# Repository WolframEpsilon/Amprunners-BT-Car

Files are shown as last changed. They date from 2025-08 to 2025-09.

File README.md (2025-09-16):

# ⚡ The Amprunners BT Car Project  
## Table of Contents
1. [Project Overview](#project-overview)  
2. [Components Used](#components-used)  
3. [Circuit Design](#circuit-design)  
4. [Code Implementation](#code-implementation)  
5. [Chassis & Assembly](#chassis--assembly)  
6. [Testing & Challenges](#testing--challenges)  
7. [Future Improvements](#future-improvements)  
8. [Credits](#credits)  

---

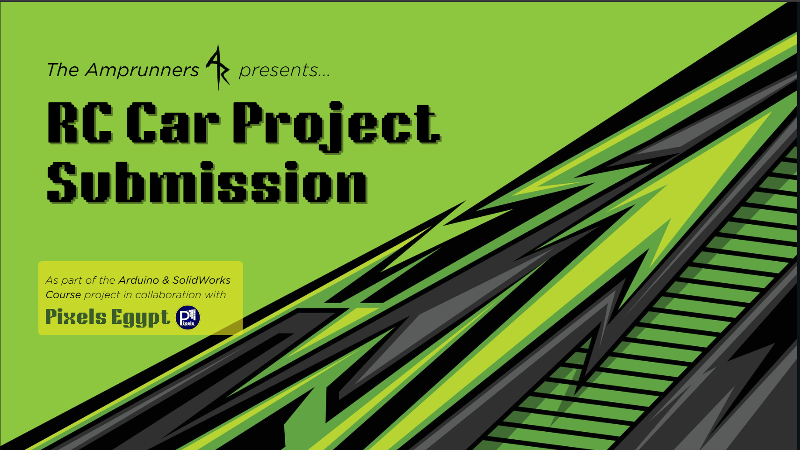
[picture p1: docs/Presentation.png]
Canva Design (https://www.canva.com/design/DAGyNDEWMuc/WyMPQTmzuohv-2UcNLUx6A/view?utlId=hdddcee9b77#1)


> A course project built to demonstrate skills in electronics, microcontroller programming, and system integration.  

---

## Project Overview
This project was developed as part of a Pixel's Embedded Arduino and SolidWorks course to design and build a working toy car.

The goal was to build two cars from scratch, control them wirelessly using:
* Bluetooth module (as used in model APEX)  
* Mobile BT App (seen in model NOVA)
  
### [📱 Amprunners Controller App (Android)](Amprunners_controller.apk)
### [🎥 Watch Demo Video (MP4)](docs/Demo.mp4)
---

## Components Used 
**3D model, wheels, chassis and assembly have their own section below*
- **Microcontroller:** Arduino Uno R3 (Car control)
- **Motor Driver:** L293D H-Bridge  
- **Motors:** 2x DC hobby motors (for RWD)
- **Steering:** SG90 micro servo motor
- **Sensors:** HC-SR04 ultrasonic (for obstacle detection)  
- **Communication:** HC-05 Bluetooth module 
- **Power:** 3.7V Li-ion battery x 3  
- **Sound:** TMB12A05 Active buzzer, KSP2222A Transistor
- **LEDs:** 3 pairs (red, white, and 3rd's your colour of choice) 
## Extra components for model APEX:
- **Control:** KY-023 PS2 joystick module
- **Microcontroller:** A second Arduino Uno R3 (Remote control) 
- **Communication:** HC-05 Bluetooth module 

---

## Circuit & System Design
#### Wiring Diagram 
- Wiring on [TinkerCAD](), or view the circuit as a [.brd file](hardware/circuit.brd)
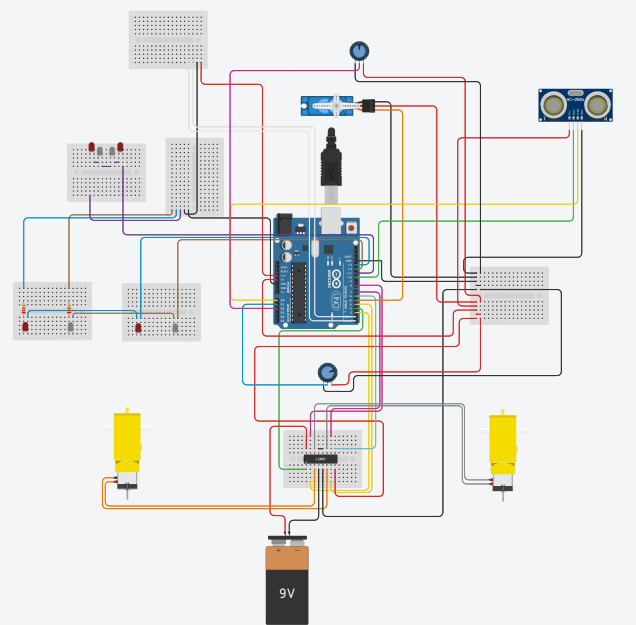
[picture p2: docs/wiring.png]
Wiring Diagram
-

#### Power distribution: 
*connecting the 3 batteries in series using a pack*

    Battery pack --> Kill switch --> H-Bridge +12V pin
    H-Bridge 5V pin --> 5V power rail --> Arduino's 5V power pin 
  <small>(more on this later)</small>  

### Pin Connections: 

##### Motors
| Component | Pin / Connection |
|---|---|
| Motor A IN1 | D3 |
| Servo Control | D4 |
| Motor A IN2 | D5 |
| Motor B IN1 | D6 |
| Motor B IN2 | D9 |

##### Comms.
| Component | Pin / Connection |
|---|---|
| BT Module Tx | D0 (MCU Rx) |
| BT Module Rx | D1 (MCU Tx) |
| Ultrasonic Trig | D8 |
| Ultrasonic Echo | A0 |

##### Others
| Component | Pin / Connection |
|---|---|
| Transistor (buzzer) | D2 |
| HeadLights | D11 |
| Reverse Lights | D12 |
| Taillights | D13 |

---

## Code
Main features of the code:
- Reads instructions from BT module/App.  
- Controls motors' speed (3 in each direction) via H-Bridge.
- Control steering via servo motor (front wheels) + one hobby motor (rear wheel)   
- Stops when obstacles are detected by ultrasonic, then starts beeping.
- Beeps periodically when backing up (like big trucks)
- Toggling on/off headlights and buzzer (horn)
- Reverse and Tail lights light up automatically according to movement 

#### *Code Snippet* 
##### [Full NOVA code available here](/src)
```cpp

switch (read){
  case 'F':  
    if(!stopFlag){
      forward(); digitalWrite(backled,LOW); digitalWrite(buzz,LOW);}
    else{
      stop(); digitalWrite(backled,HIGH); buzzAlert();}
      break;

  case 'B': 
    digitalWrite(backled,LOW); backward(); buzzRev(); ledRev(); 
    break;  
``` 
<sub>IDE: Arduino IDE 
Libraries: Servo.h   
Board: Arduino Uno R3   
Baud rate: 9600 baud   
</sub>   

---

## Chassis & Assembly 
Our team agreed on making the car RWD, rather than AWD; simply because it was more economical

> Using [this model](https://www.thingiverse.com/thing:4772279) made by Pammeg80 on Thingiverse.com as our inspiration , with some slight adjustments

#### Alterations to base model:
1. Made a small hole using SolidWorks to fit the pins for the ultrasonic sensor
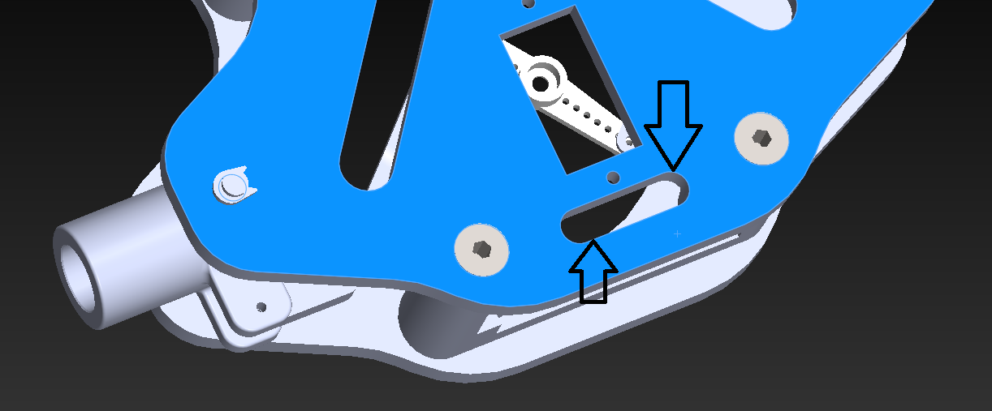
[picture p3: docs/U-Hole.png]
Ultrasonic Hole adjustment
-

2. Removed the 9V power at the back, while mounting the 12V pack (mentioned here) under the model 
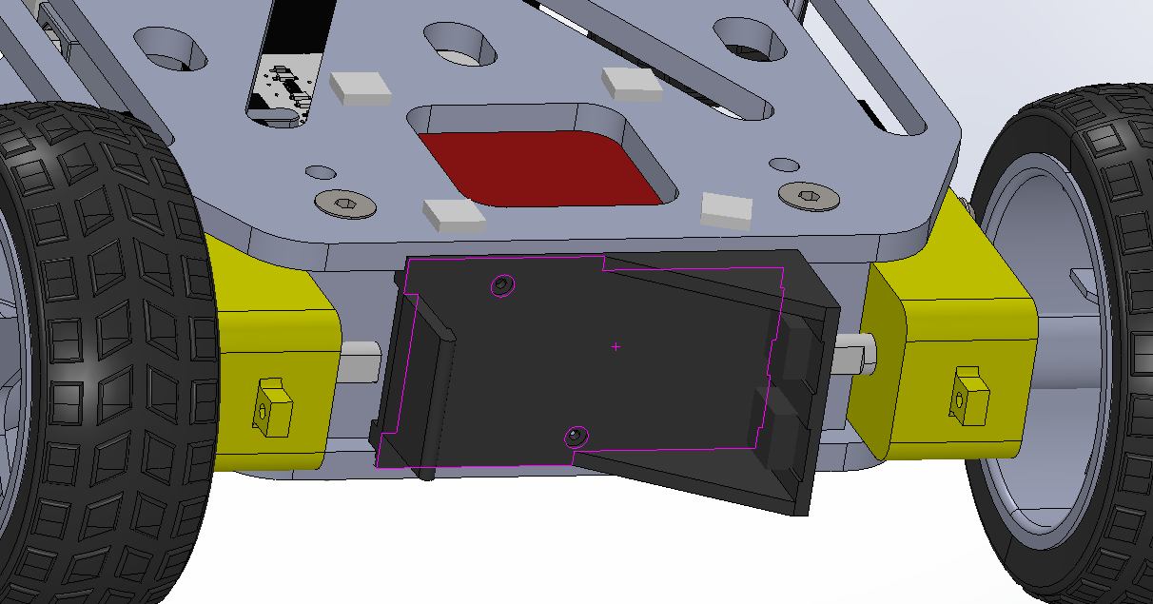
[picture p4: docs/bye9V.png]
9V removal
-

3.  Adding a nameplate for visuals with a "THOMAS" text ingravement + LED Holes 
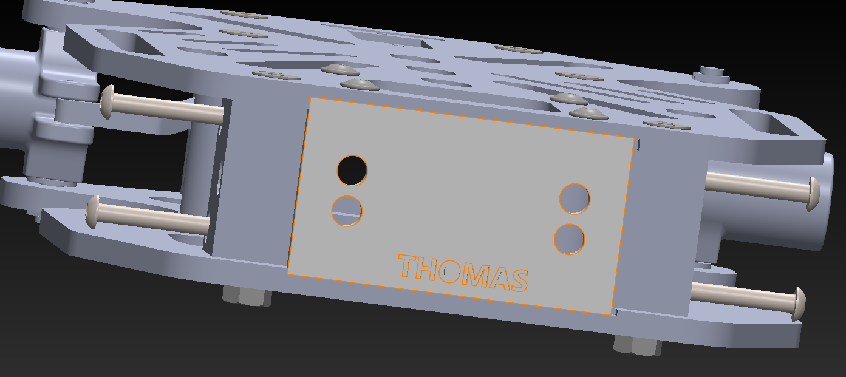
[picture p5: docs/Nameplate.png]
Thomas Nameplate
-

4. Small pillars to hold headlight's LEDs (Not saved unfortunately)  

---

## Testing
### Phase 1: Wiring test
This was done by adding a Keyboard (of varing resistance) to one analogue pin, and manually taking resistance reading to form a resistance-to-key map.
The following map was created:

```cpp
//Keypad Resistance Map//
#define ast_KEY 47
#define zero_KEY 51
#define hash_KEY 57
#define seven_KEY 60
#define D_KEY 64
#define eight_KEY 68
#define nine_KEY 79
#define four_KEY 85
#define C_KEY 93
#define five_KEY 102
#define six_KEY 128
#define one_KEY 146
#define B_KEY 171
#define two_KEY 205
#define three_KEY 341
#define A_KEY 1023

#define keyPin A1 //where i received the key strokes
```

Analogue pins are know to give a range of values due to external factors, like temperature changes messing with the resistance reading
So a tolerance range was added to compensate for this error as shown in this function:

```cpp
//funcion for reading the keypad-resistance configuration//
char KeypadReading() {
  int val = analogRead(keyPin);

  // sorted in ascending order with tolerances of 2~4//
  if (val < 44) return 0;  //null if not in range//  
  else if (val < 49) return '*';
  else if (val < 53) return '0';
  else if (val < 59) return '#';
  else if (val < 62) return '7';
  else if (val < 66) return 'D';
  else if (val < 70) return '8';
  else if (val < 82) return '9';
  else if (val < 88) return '4';
  else if (val < 96) return 'C';
  else if (val < 105) return '5';
  else if (val < 132) return '6';
  else if (val < 150) return '1';
  else if (val < 175) return 'B';
  else if (val < 210) return '2';
  else if (val < 345) return '3';   
  else if (val > 1000 && val <= 1023) return 'A';

  return 0; //again, null if not in range//
}
``` 

### Phase 2: Joystick Implementation
Using a potentiometer (10K Ohm) for steering control, and another (10K Ohm) for motor speed we constructed the following circuit:
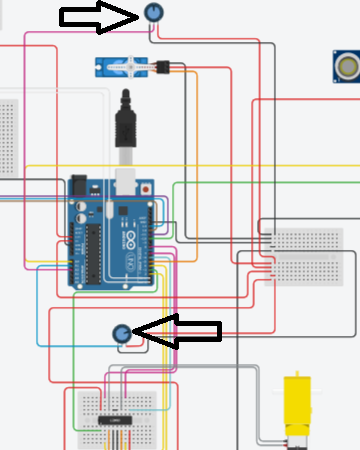
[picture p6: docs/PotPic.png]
Potentiometer circuit
-   

and controlled their movement using the code below: 
```cpp
  int steer = map(analogRead(steerPot),0,1023,0,180); //joystick reading for servo
  int drive = map(analogRead(hobbyPot),0,1023,0,255); //joystick reading for motor
  
  Serial.print("steer= ");
  Serial.print(steer);
  Serial.print("||drive= ");
  Serial.println(drive);
  
  //-----front and back in 3 levels each-----//
  if(drive == 128) {  // ~centered
    digitalWrite(backLED,HIGH);  //not moving
    digitalWrite(reverseLED,LOW); //reverse-light off
  }
  else if(drive > 128){ //going forwards
    forwards(drive); 
    digitalWrite(backLED,LOW); //break-light off
    digitalWrite(reverseLED,LOW); //reverse-light off
  }
  else if(drive < 128){ //going backwards
    backwards(drive); 
    digitalWrite(backLED,LOW); //break-light off
    digitalWrite(reverseLED,HIGH); //reverse-light on
  }

  //-----right and left-----//
  steerMotor.write(steer);
```

---

## Challenges (and how we overcame them)

## 1. 12V power to 5V Arduino:
#### Issue:
>* Feeding 12V into the arduino power plug would instantly fry the circuit
>* using multiple power sources would be inefficient and require extra wiring complexity
>* Linear voltage regulator need comprehensive understanding (in a small time period)
### Solution: H-bridge power supply
Surprisingly, the **L293D H-Bridge** model has a neat feature activated by adding a jumper cap to a built-in voltage regulator; allowing +12V power to motors and feeding just 5V from it's power slot (normally used to power the module itself)

## 2. H-bridge driving wheels incorrectly
This manifested as both RWD motors being able to move backwards, but motor A (left) failing to drive forwards
#### Cause: 
>Instability from mechanical vibration of motors; resulting in lose conections
#### Solution: Physically fixing connections and insulation
using a hot soldering iron and lead, we were able to Solder connections well, and prevent shorts using Heat shrink tubing at exposed locations

## 3. Car wheels not fitting into chasis
#### Cause:
>no tolerances added during modelling; which lead to an impossible interference fit
#### Solution: Tolerance adjustment 
fortunately, we had a drill bit that was exactly the same size as the wheel, so we manually drilled through 

## 4. Irresponsive Bluetooth Pair (with remote control)
#### Cause:
>modules aren't always recognised by smart devices at specific ports, and won't go into pair or AT mode when enabled by pin
#### Solution: Changing baud rate 
It's more of a compatability problem across devices where serial communication is set out of sync, eg. 9600 baud Uno with 11600 BT module

## Other challenges
- Servo motor torque limitations occasionally caused unintended steering drift (sometimes leading to unplanned donuts 😅)
  -Thomas going wild

- Connecting pins and general wiring in the chassis; which is an extremely small area, sometimes inaccessible without t6aking the whole thing apart again

- Weak arduino pin connection, affected by the motors' vibration 

- Exposed wiring <small> (in future improvements) </small>
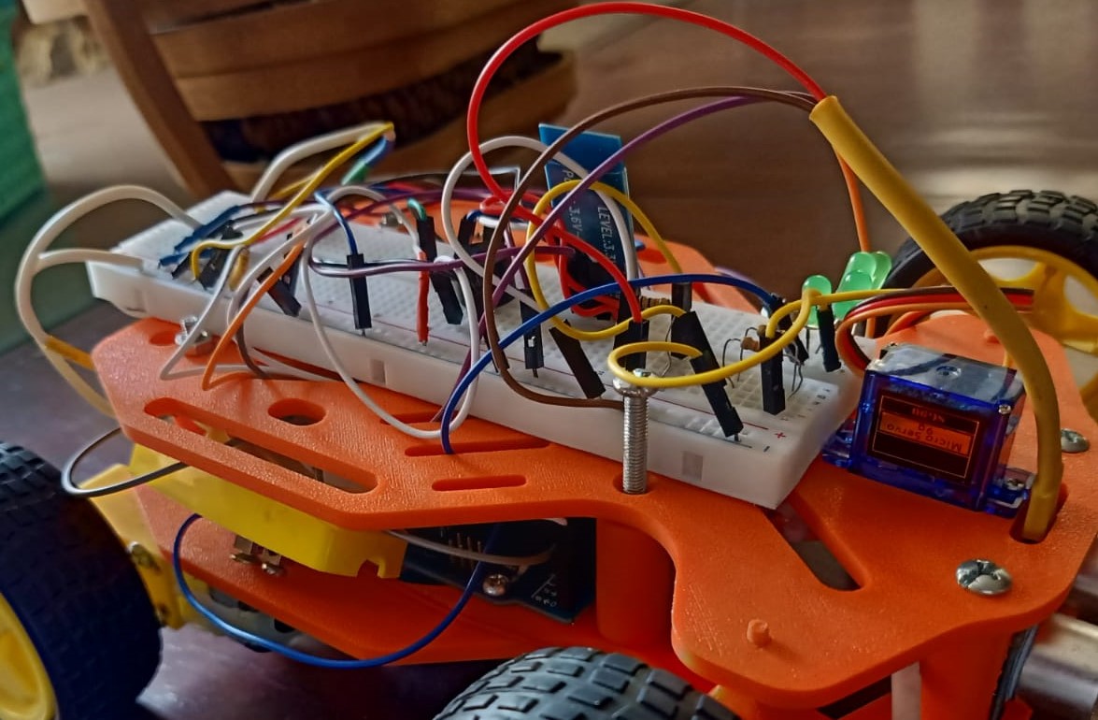
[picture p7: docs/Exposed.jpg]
Exposed
  -
---

## Future Improvements
### 1. Using an ESP32 MCU
- Built-in BT and WiFi
- More pins and faster clock speed
- Smaller footprint in an already crammed area
### 2. 3D Printing the car's original body
We didn't have the time to assemble this part withing the deadline, but we do have the model (pulled from Rocket League by [Paul Ashley on GrabCAD](https://grabcad.com/library/all-rocket-league-car-object-files-a-few-bonus-s-1)):
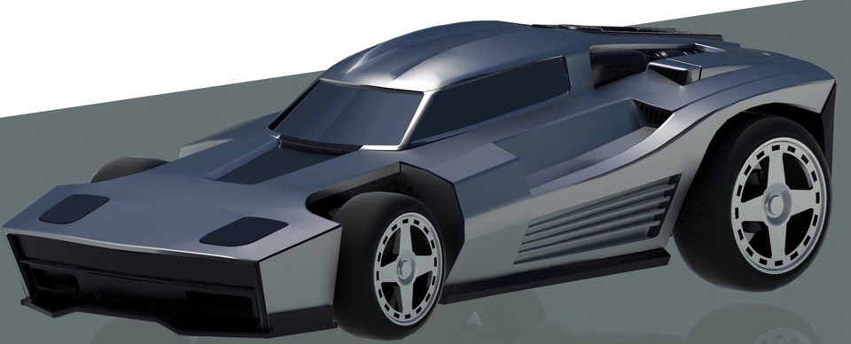
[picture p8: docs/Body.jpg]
Body
  -
### 3. Backwards Obstacle Detection
reducing impact possibility, thus improving lifespan 
### 4. Surface-mounted robotic arm  
for object transportation, perhaps in warehouses
### 5. Infrared light sensor
for line follower feature
### 6. Camera Module
for object distinction or QR code scanning

---

## Credits
#### [Omar M. Gobara](www.linkedin.com/in/omargobara/)
* Full Simulation (TinkerCAD)
* Final Assembly & Code Polishing
* Documentation (this one) 
* Body prototype

#### [Ahmed I. Madkour](https://www.linkedin.com/in/ahmedimadkour/)
* 3D modelling (SolidWorks) & Printing
* initial Assembly & Code integration
* Project management & Team coordination
* Cosmetics Design (Presentation, Logos, IDs, etc.)

#### [Kerollos Mekhail](https://www.linkedin.com/in/kerollos-mekhail-gad/) 
* Lead Custom application developer (MIT App Inventor)
* Car BT Communication Subsystem
* Car Speed Subsystem

* intermediate Code developer

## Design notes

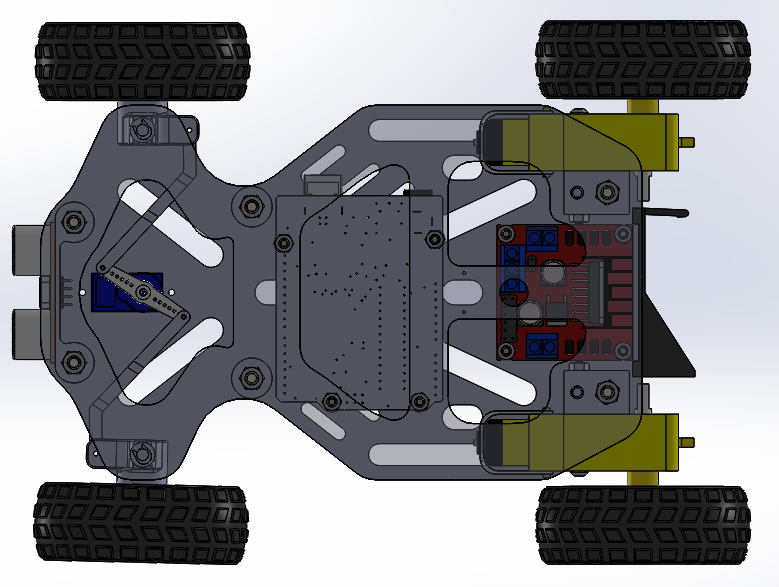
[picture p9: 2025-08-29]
car4.PNG

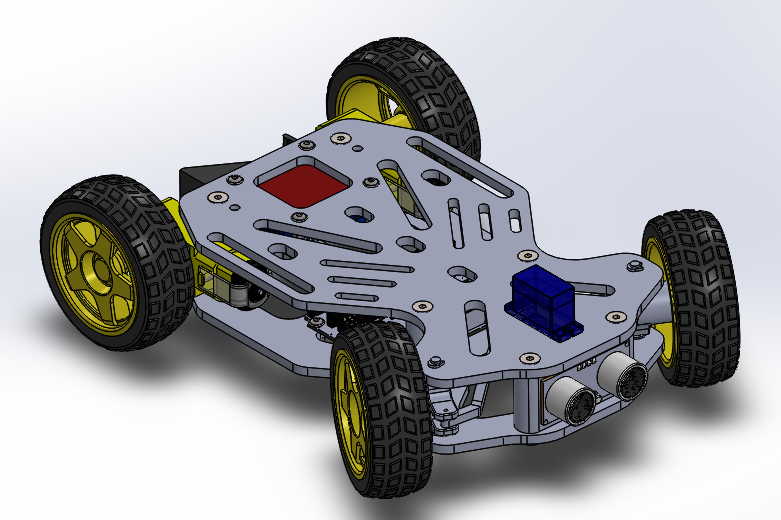
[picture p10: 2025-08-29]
car1.PNG

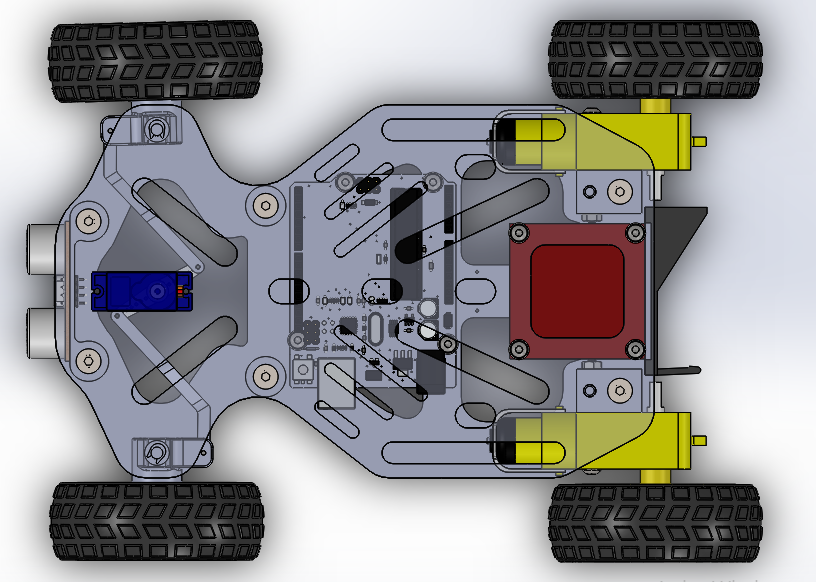
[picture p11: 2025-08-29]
car5.PNG

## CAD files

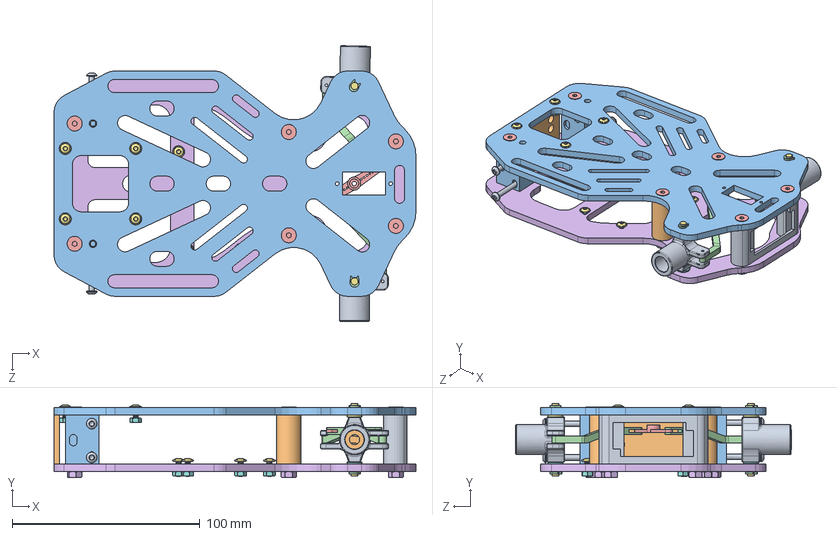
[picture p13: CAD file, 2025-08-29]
models/APEX&NOVA/Final_THOMAS.SLDASM
192.7 x 39.5 x 146.8 mm
mozzo1 x 2
Semiasse1 x 2
Chassis2
barra_sterzo3 x 2
microservoArm(A2)
Copri_Chassis2
perno_sterzo x 2
spessore_sterzo x 2
mascherina
colonnetta x 2
supporto_motore2 x 2
seeger3 x 4
DIN7991_M4x35(ISO 7991 M04 x 20) x 6
M4 Nut x 6
DIN_EN_ISO_7380_M3x8.ipt x 8
M3 Nut x 12
ISO 7380_M3x35(ISO 7380 - M3 x 10) x 4

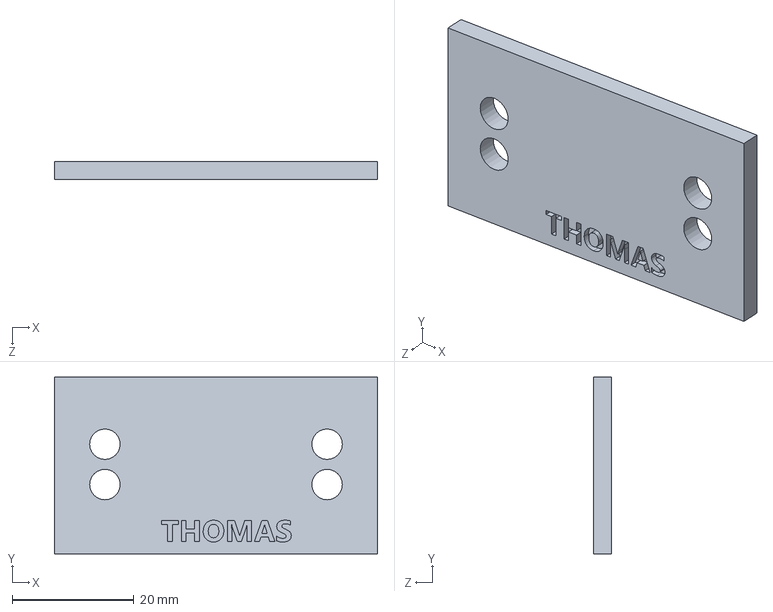
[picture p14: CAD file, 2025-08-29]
models/APEX&NOVA/Part53.SLDPRT
53.0 x 29.0 x 3.00 mm

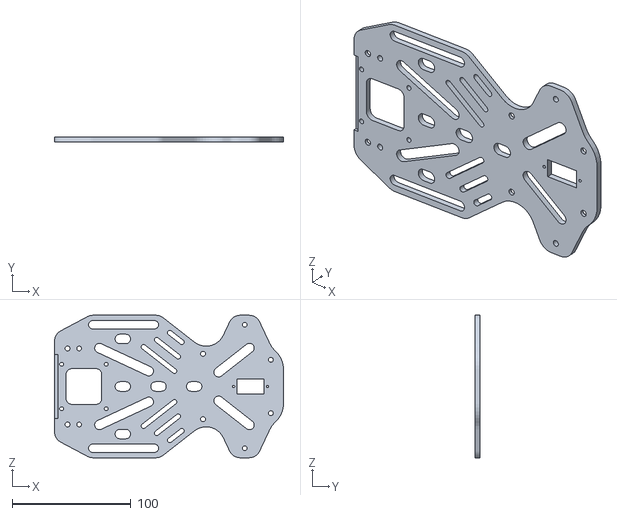
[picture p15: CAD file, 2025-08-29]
models/APEX&NOVA/Chassis_UP.STL
192.7 x 4.00 x 120.0

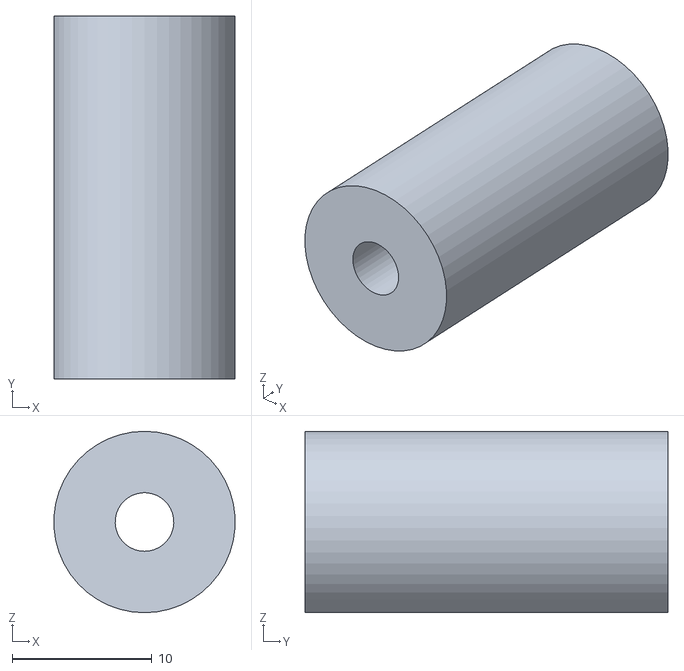
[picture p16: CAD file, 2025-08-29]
models/APEX&NOVA/spacer.STL
13.0 x 26.0 x 13.0

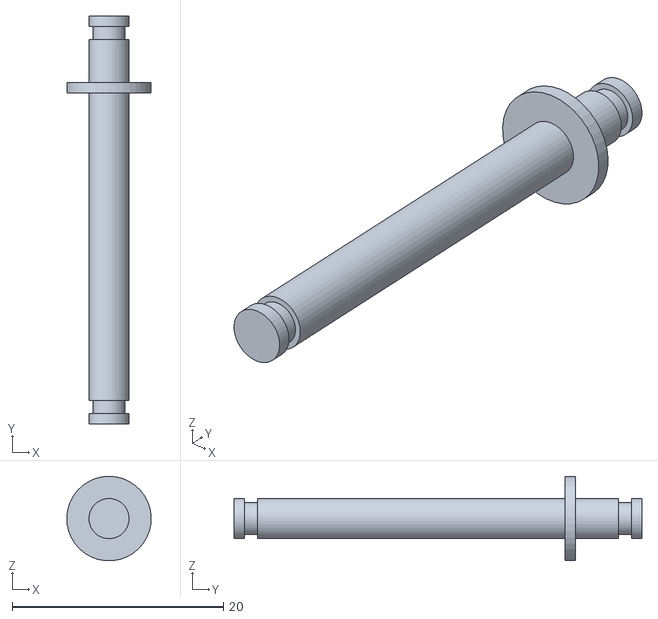
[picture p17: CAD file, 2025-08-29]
models/APEX&NOVA/pivot_hub.STL
7.99 x 38.6 x 7.99

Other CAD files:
models/APEX&NOVA/microservoAssembly.SLDASM
models/APEX&NOVA/Assieme3^Macchina_2_sterzante.SLDASM
models/APEX&NOVA/Assieme3^Macchina_2_sterzante-1.SLDASM
models/APEX&NOVA/Ruota_ant_sterzante.SLDASM
models/APEX&NOVA/Ruota_ant_sterzante-1.SLDASM
models/APEX&NOVA/DIN_EN_ISO_7380_M3x8.ipt.SLDPRT
models/APEX&NOVA/microservoSG90.SLDPRT
models/APEX&NOVA/spessore_sterzo.SLDPRT
models/APEX&NOVA/Motor_Gear_Box.SLDPRT
models/APEX&NOVA/seeger3.SLDPRT
models/APEX&NOVA/Wheel D65x25.SLDPRT
models/APEX&NOVA/perno_sterzo.SLDPRT
models/APEX&NOVA/mozzo1.SLDPRT
models/APEX&NOVA/Chassis2.SLDPRT
models/APEX&NOVA/Chassis_DOWN.STL
models/APEX&NOVA/Copri_Chassis2.SLDPRT
models/APEX&NOVA/DIN7991_M4x35(ISO 7991 M04 x 20).SLDPRT
models/APEX&NOVA/Frontal.STL
models/APEX&NOVA/HC-06.SLDPRT
models/APEX&NOVA/Hub_front.STL
models/APEX&NOVA/ISO 7380_M3x35(ISO 7380 - M3 x 10).SLDPRT
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
